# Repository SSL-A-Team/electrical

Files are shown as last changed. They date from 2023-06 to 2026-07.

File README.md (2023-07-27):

# Getting Started with A-Team Electrical

All current board releases use KiCad 7.X. 

See [releases](https://github.com/SSL-A-Team/electrical/releases) for competition production files. Our releases include known bug documentation, and the confirmed gerber, BoM, and CPL files sent to fab so you know you're looking and ordering what we did. Releases are accompanied by a tagged commit, for all editable project files used to generate the fab products.

For complex boards like control and kicker, we include spice models and python files that compute any relevant values from datasheets, and including documented references and links to needed formulations. 

## Setting Up KiCAD

### Setting Up the KiCAD Library Path
- Click `Preferences->Configure Paths`
- Under `Environment Variables` click `+`
- Set the name `LIB_DIR_AT`
- Set the path to `<repository_location>/lib` where \<repository_location\> is the download location.

Example entry:
- Name: `LIB_DIR_AT`
- Path: `C:\Users\guyfl\Documents\A-Team\electrical\lib`

### Setting Up JLCPCB Plugin

KiCAD version 6.99 (nightly) or newer should install the [KiCAD JLCPCB Tools](https://github.com/Bouni/kicad-jlcpcb-tools) plugin. 

## Setting Up the Python Environment
 1. We recommend creating a python environment using `python3 -m venv venv` (python 10 appears to be required)
 2. Install poetry `pip install poetry`
 3. Run any python file with `poetry run python <python_file>`
 4. (Optional) Add dependencies with `poetry add <dependency>`

## Soldering

Our [soldering process](SOLDERING.md) is documented. Advanced components like modern SMPS chips and current sense motor hardware proved sensitive to technique. The team's tries to PCBA as much as possible, but sometime it's too expensive to PCBA all chips, especially advanced ones not in stock at the fab house.

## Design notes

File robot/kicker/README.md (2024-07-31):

# Kicker Boards

Subfolders contain various versions of the kicker board. A summary is included below.

## Kicker Version Summary

 - v1.1.0_fe - Nonviable, check errata
 - v1.1.0_ufd - Nonviable, check errata
 - v1.0.0 - Nonviable, check errata
 - v2.0.0 - Patchable, check errata
 - v3.0 - Patchable, check errata
 - v3.1 - Functional, minor patching suggested

## KiCad Version Summary

 - v3.1 - KiCad v7.X
 - v3.0 - KiCad v7.X
 - v2.0.0 - KiCad v7.X
 - v1.1.0 - KiCad v7.X
 - v1.0.0 - KiCad v6.99 (nightly)

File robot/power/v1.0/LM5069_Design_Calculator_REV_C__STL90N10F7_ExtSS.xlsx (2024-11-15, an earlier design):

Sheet: Instructions
 | © 2014
LM5069 Design Tool- Rev. C
Typical design procedure
Typical applications require multiple passes through the design tool using MOSFET factors such as transient
thermal response and safe operating area curves. Refer to the following application reports for more detail.
Robust Hot Swap Design (http://www.ti.com/lit/pdf/slva673)
LM5069 Datasheet (See "Design-In Procedure") (http://www.ti.com/lit/gpn/lm5069)
The basic design process follows:
1. Enter operating conditions.
2. Select current limit parameters.
3. Enter MOSTFET SOA characteristics & power limit.
4. Select start up conditions (load and/or soft start). Check whether FET is operating with reasonable margin, within the SOA curve.
If not, try changing start-up conditions (soft start values, timer values), add more FETs in parallel, or switch to FET with better SOA.
5. Enter desired UVLO and OVLO values to get recommended resistor values.
6. Done
Notes
1. This worksheet is designed for use with Microsoft Excel 5.0 or later. Its use is intended to assist power supply designers in their
routine, day-to-day calculations.
2. All worksheets have light green inputs cells, white calculated cells, yellow warning cells and red high-risk cells.
3. Formulas and device constants used in the spreadsheet are locked to prohibit them from accidentally being overwritten or deleted.
TEXAS INSTRUMENTS TEXT FILE LICENSE Copyright (c) 2014 Texas Instruments Incorporated All rights reserved not granted herein. Limited License. Texas Instruments Incorporated grants a world-wide, royalty-free, non-exclusive license under copyrights and patents it now or hereafter owns or controls to make, have made, use, import, offer to sell and sell ("Utilize") this software subject to the terms herein. With respect to the foregoing patent license, such license is granted solely to the extent that any such patent is necessary to Utilize the software alone. The patent license shall not apply to any combinations which include this software, other than combinations with devices manufactured by or for TI (“TI Devices”). No hardware patent is licensed hereunder. Redistributions must preserve existing copyright notices and reproduce this license (including the above copyright notice and the disclaimer and (if applicable) source code license limitations below) in the documentation and/or other materials provided with the distribution Redistribution and use in binary form, without modification, are permitted provided that the following conditions are met: * No reverse engineering, decompilation, or disassembly of this software is permitted with respect to any software provided in binary form. * any redistribution and use are licensed by TI for use only with TI Devices. * Nothing shall obligate TI to provide you with source code for the software licensed and provided to you in obje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

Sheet: Design Calculator
LM5069 Hot Swap Design Tool
 | www.ti.com/hotswap
 |  |  | Enter Values in Green Shaded Cells
 |  |  | Calculated Values are shown in White Cells
 |  |  | Yellow and Red cells highlight potential issues with the design. Red highlights items that are higher risk.
 | Step 0: Calculator Tutorials |  | Note: Before proceeding, please watch the video tutorials listed to ensure accurate results from this tool!
 |  |  | Steps 1 & 2: Operating Conditions, Current Limit, & Circuit Breaker (7:41) (https://training.ti.com/node/1133677)
 |  |  | Step 3: MOSFET Selection (9:58) (https://training.ti.com/node/1133673)
 |  |  | Step 4: Startup (10:32) (https://training.ti.com/node/1133664)
 |  |  | Step 5: UVLO, OVLO & PGD Thresholds (4:20) (https://training.ti.com/node/1133681)
 |  |  | LM5069 Datasheet (http://www.ti.com/product/lm5069)
 |  |  | I understand and agree to watch the video tutorials if help is needed. (Choose Yes to enable the calculator.) |  |  | Yes
 |  |  | Assure to follow the layout and application guidelines listed on the datasheet. |  |  | Yes
 |  |  | *For additional questions not addressed in the videos, please post on E2E.ti.com
 | Step 1: Operating Conditions |  |  | Minimum Input Operating Voltage: VIN(MIN) | 15 | V
 |  |  |  | Nominal Input Operating Voltage: VIN(NOM) | 22.2 | V
 |  |  |  | Maximum Input Operating Voltage: VIN(MAX) | 25.2 | V
 |  |  |  | Maximum Load Current: IOUT(MAX) | 29 | A
 |  |  |  | Maximum Output Load Capacitance: CLOAD | 1500 | µF
 |  |  |  | Maximum Ambient Operating Temperature: TMAX | 45 | oC
 | Steps 1 & 2: Operating Conditions, Current Limit, & Circuit Breaker (https://training.ti.com/node/1133677)
 | Step 2: Current Limit and Circuit Breaker |  |  | Current Limit Threshold Voltage | 55 mV
 |  |  |  | Maximum Recommended Value for Effective Sense Resistance | 1.66 | mW
 |  |  |  | Use External Resistor Divider to Reduce Effecitve RS | No |  |  |  |  |  | Yes
 |  |  |  | Enter the Resistance for RS | 1.5 | mW |  |  |  |  | No
 |  |  |  | Recommended Value for RCL1 | NA | W
 |  |  |  | Recommended Value for RCL2 | NA | W
 |  |  |  | Enter value for RCL1 | 10 | W |  |  |  |  | TRUE
 | Steps 1 & 2: Operating Conditions, Current Limit, & Circuit Breaker (https://training.ti.com/node/1133677) |  |  | Enter value for RCL2 | 3.04 | W
 |  |  |  | Effective Sense Resistance (RS,EFF) | 1.50 | mW
 |  |  |  | Resulting Minimum Current Limit | 32.3 | A
 |  |  |  | Resulting Typical Current Limit | 36.7 | A
 |  |  |  | Resulting Maximum Current Limit | 41.0 | A |  |  |  |  | Retry
 |  |  |  | Maximum Power Dissipation in RS | 2.5 | W |  |  |  |  | Latch Off
 |  |  |  | Fault Response | Retry |  |  |  |  |  | 1.9 x Current Limit
 |  |  |  | Circuit Breaker to Current Limit Raitio | 1.9 x Current Limit |  |  |  |  |  | 3.9 x Current Limit
 | Step 3: MOSFET Selection |  |  | Q1 FET Name | STL90N10F7
 |  |  |  | Estimated MOSFET RQJA | 31 | oC/W |  |  |  |  | 9.978699315 | 4.193548387
 |  |  |  | Number of MosFETs | 2 | # |  |  |  |  | Values Used
 |  |  |  | MOSFET On resistance @ TJ,DC | 8 | mW |  |  |  |  | 8
 |  |  |  | Maximum FET Junction Temperature | 175 | oC |  |  |  |  | 175
 |  |  |  | 100ms SOA Current (re-use 1ms data if unavailable) @ VIN(MAX) | 55 | A |  |  |  |  | 55
 | Step 3: MOSFET Selection (https://training.ti.com/node/1133673) |  |  | 1ms SOA Current @ VIN(MAX) | 27 | A |  |  |  |  | 27
 |  |  |  | 10ms SOA Current @ VIN(MAX) | 4 | A |  |  |  |  | 4
 |  |  |  | 100ms Current at @ VIN(MAX) (enter 'NA' if not available) | NA | A |  |  |  |  | NA
 |  |  |  | 1s or DC SOA Current at @ VIN(MAX) (enter 'NA' if not available) | NA | A |  |  |  |  | NA
 | Note: TI recommends choosing a FET with SOA current specified for 100ms and/or 1s or DC. If choosing a FET without these parameters, this calculator will estimate the values via extrapolation, which leaves an inherent associated risk. |  |  | FET Power dissapation at full load (per FET) | 1.7 | W
 |  |  |  | Maximum steady state FET Junction Temperature (TJ,DC) | 97.1 | oC
 |  |  |  | Minimum Power Limit to Ensure Vsns > 5mV (PLIM,MIN) | 84.0 | W
 |  |  |  | Target Power Limit | 126.00 | W
 |  |  |  | Calculated RPWR | 23.62 | kW
 |  |  |  | Actual RPWR | 16.2 | kW | Note: Hover here to see the 3 values affecting this curve, consult a thermal expert if you are unsure!
 |  |  |  | Actual PLIM | 86.40 | W
 | Step 4: Startup |  |  | Load Turn-On Threshold | 0 | V
 |  |  |  | Startup Load Type | Constant Current
 |  |  |  | Startup Load Value | 0 | A |  |  |  |  | Constant Current
 |  |  |  | Use External Soft-Start Control (dv/dt) | Yes |  |  |  |  |  | Resistive
 |  |  |  | Typical Start Time with Vinmax (Tstart) | 157.50 | ms
 |  |  |  | IFET - ILOAD margin (lowest for Vout range) | 100%
 |  |  |  | Target Fault Timer: Tstart + Margin | 236.25 | ms
 |  |  |  | Target Timer capacitance | 5020.31 | nF
 |  |  |  | Selected Timer capacitance | 220 | nF
 |  |  |  | Final Fault Timer(Tfault) | 10.35 | ms
 | Step 4: Startup (https://training.ti.com/node/1133664) |  |  | Derated SOA / PLIM | 2.84
 |  |  |  | Can a "hot" board be hotplugged | Yes
 |  |  |  | Recommended slew Rate (max) | 0.22 | V/ms
 |  |  |  | Recommended slew Rate (min) | 0.11 | V/ms
 |  |  |  | dv/dt rate on Vout | 0.15 | V/ms
 |  |  |  | calculated SS capacitance | 106.67 | nF
 | Note: This is the typical dv/dt rate, but max value can be 1.4x. This is because the gate source current can vary from 16uA to 22uA. Thus TI recommends keeping the overall SOA margin during start-up >1.5 in order to compensate for this. |  |  | actual SS capacitance | 100 | nF
 |  |  |  | actual typical dv/dt rate on Vout | 0.16 | V/ms
 |  |  |  | SOA margin during start-up | 1.57
 |  |  |  | Target Fault Time | 0.52 | ms
 |  |  |  | Calculated Timer Capacitance | 11.05 | nF
 |  |  |  | Actual Timer Capacitance ( pick one smaller than CT,CALC) | 33 | nF
 |  |  |  | Actual Fault Time (Tfault) | 1.55 | ms
 |  |  |  | SOA margin during "hot-short" or "start-into short" | 2.84
 |  |  |  | Resulting Typical Insertion Delay Time | 24 | ms
 |  |  |  | Resulting Typical Restart Time | 310.41 | ms
 | Step 5: UVLO, OVLO & PGD Thresholds |  |  | Select Option A or Option B | Option B |  |  |  |  |  | Option A
 |  |  |  | Desired Upper UVLO Threshold | 16 | V |  |  |  |  | Option B
 |  |  |  | Desired Lower UVLO Threshold | 15 | V |  |  |  |  | Option C
 |  |  |  | Desired Upper OVLO Threshold | 30 | V |  |  |  |  | Option D
 |  |  |  | Desired Lower OVLO Threshold | 28 | V
 |  |  |  | Recommended Resistance for: R1 | 47.62 | kW
 |  |  |  | R2 | 9.52 | kW
 | Step 5: UVLO, OVLO & PGD Thresholds (https://training.ti.com/node/1133681) |  |  | R3 | 95.24 | kW
 |  |  |  | R4 | 8.66 | kW
 |  |  |  | Enter the Resistance for R1 | 47.5 | kW
 |  |  |  | Enter the Resistance for R2 | 9.53 | kW
 |  |  |  | Enter the Resistance for R3 | 95.3 | kW
 |  |  |  | Enter the Resistance for R4 | 8.66 | kW
 |  | Resulting Thresholds: | Minimum | Typical | Maximum
 |  | Resulting Upper UVLO Threshold = | 15.23 | 15.96 | 16.68 | V
 |  | Resulting Lower UVLO Threshold = | 14.66 | 14.96 | 15.26 | V
 |  | Resulting Upper OVLO Threshold = | 29.41 | 30.01 | 30.61 | V
 |  | Resulting Lower OVLO Threshold = | 26.55 | 28.01 | 29.47 | V
 |  | Note: If any of the cells above are yellow, then these values are outside of the device's operating range. This will result in the device turning either on or off at its operating limits rather than at the user selected values in yellow.
 |  |  |  | Enter the Resistance for RPG | 1500 | kW
 | Design Summary |  |  | RSNS = | 1.5 | mW
 |  |  |  | RCL1 = | DNP | W
 |  |  |  | RCL2 = | 0 | W
 |  |  |  | RPWR = | 16.2 | kW |  |  | Settings | Units
 |  |  |  | CTIMER = | 33.00 | nF |  | Current limit | 36.7 | A
 |  |  |  | R1 = | 47.5 | kW |  | Power Limit | 86.4 | W
 |  |  |  | R2 = | 9.53 | kW |  | Circuit Breaker Current | 36.7 | A
 |  |  |  | R3 = | 95.3 | kW |  | Startup Time | 157.50 | ms
 |  |  |  | R4 = | 8.66 | kW |  | Insertion Delay | 24.0 | ms
 |  |  |  | Cdv/dt = | 100 | nF |  | Fault Timeout | 1.55 | ms
 |  |  |  | CIN = | 0.01 | µF |  | Restart Time During Fault | 310.414 | ms
 |  |  |  | D1 | B380-13-F |  |  | Upper UVLO Threshold | 15.958 | V
 |  |  |  | D2 | 1N4148W-7-F |  |  | Lower UVLO Threshold | 14.961 | V
 |  |  |  | Q1 | STL90N10F7 |  |  | Upper OVLO Threshold | 30.012 | V
 |  |  |  | Q2 | MMBT5401LT1G |  |  | Lower OVLO Threshold | 28.010 | V
 |  |  |  | Z1 | 5.0SMDxx
 | Notes: | 1. Although not mandatory, CIN provides transient suppression at the VIN pin
 |  | 2. A TVS clamp from VIN to GND is absolutely mandatory to clamp the voltage overshoot upon MOSFET turn-off, e.g. during circuit breaker
 |  | 3. Componet tolerances not accounted for in Min/Max Calculations.

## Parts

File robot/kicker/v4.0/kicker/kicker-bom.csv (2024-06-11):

Comment | Designator | Footprint
10u 100V | C1, C2 | Capacitor_SMD:C_1210_3225Metric
100n 50V | C3, C4, C5, C26, C29, C34, C35, C36, C37, C38, C40, C41, C46, C48, C49, C54, C55, C56, C57, C58, C59, C61, C68, C69 | Capacitor_SMD:C_0402_1005Metric
4.7n 63V | C6 | Capacitor_SMD:C_0402_1005Metric
10n 6.3V | C7, C8, C45, C47 | Capacitor_SMD:C_0402_1005Metric
470n 6.3V | C9, C10 | Capacitor_SMD:C_0402_1005Metric
1n 50V | C11, C12, C13, C14 | Capacitor_SMD:C_0402_1005Metric
1u 50V | C15, C16, C17, C18, C23, C24, C25, C39 | Capacitor_SMD:C_0402_1005Metric
10u 25V | C19, C20, C21, C22 | Capacitor_SMD:C_0603_1608Metric
11pF | C27, C28 | Capacitor_SMD:C_0402_1005Metric
4.7u 6.3V | C30, C31, C32, C33, C44 | Capacitor_SMD:C_0402_1005Metric
15pF | C42, C43 | Capacitor_SMD:C_0402_1005Metric
10u 6.3V | C50 | Capacitor_SMD:C_0402_1005Metric
1000uF 200V | C51, C52, C53 | Capacitor_THT:CP_Radial_D25.0mm_P10.00mm_SnapIn
10u 50V | C60, C64, C66, C67, C70, C72 | Capacitor_SMD:C_0805_2012Metric
220u 50V | C62, C63 | Capacitor_SMD:CP_Elec_10x10
10n 50V | C65 | Capacitor_SMD:C_0402_1005Metric
6.8n 50V | C71 | Capacitor_SMD:C_0402_1005Metric
4.7u 50V | C73 | Capacitor_SMD:C_0805_2012Metric
100n 200V | C74 | Capacitor_SMD:C_0805_2012Metric
100n 500V | C75 | Capacitor_SMD:C_1210_3225Metric
470n 500V | C76, C77 | Capacitor_SMD:C_1812_4532Metric
824521261 | D1, D2 | AT-Discrete:D_SMB_Non-Polar
XL-1608UWC-04 | D3 | AT-LED:LED0603
DSS14U | D4, D5, D6, D7 | Diode_SMD:D_SOD-123F
XL-1608SURC-06 | D8, D13 | AT-LED:LED0603
PESD3V3L5UY | D9 | Package_TO_SOT_SMD:SOT-363_SC-70-6
XL-1608UBC-04 | D10, D11 | AT-LED:LED0603
XL-1608UGC-04 | D12 | AT-LED:LED0603
XL-1608UOC-06 | D14 | AT-LED:LED0603
APA1606SURCK | D15, D16 | AT-LED:APA1606
MURS460 | D17, D18 | Diode_SMD:D_SMC
HS5M | D19 | Diode_SMD:D_SMC
15A | F1 | AT-Fuses:3557-2
1.0A | F2, F3, F4, F5 | Fuse:Fuse_0603_1608Metric
9774005243R | H3, H4, H7, H8 | AT-Mechanical:WE-9774005243R
Conn_ARM_JTAG_SWD_10 | J2 | AT-Connectors:Samtec-2x5pin-0.5mm
Conn_01x02 | J3 | Connector_JST:JST_SH_SM02B-SRSS-TB_1x02-1MP_P1.00mm_Horizontal
Conn_01x04_Pin | J4 | Connector_PinHeader_2.54mm:PinHeader_1x04_P2.54mm_Vertical
Conn_01x10 | J5, J6, J9, J16 | Connector_JST:JST_SH_SM10B-SRSS-TB_1x10-1MP_P1.00mm_Horizontal
Conn_01x02 | J7, J8 | AT-Connectors:2157601002
Conn_01x02 | J10 | AT-JST_PA:SM02B-PASS-TBT
Conn_01x08 | J11, J14, J15 | Connector_JST:JST_SH_SM08B-SRSS-TB_1x08-1MP_P1.00mm_Horizontal
Conn_01x03 | J12, J13 | Connector_JST:JST_SH_SM03B-SRSS-TB_1x03-1MP_P1.00mm_Horizontal
ASPI-6045S-220M-T | L1 | AT-Inductors:ASPI-6045S
SDCHA1V5040-150-R | L2, L3, L4, L5 | AT-Inductors:SDCHA1V50
650 @100MHz | L6 | Resistor_SMD:R_0603_1608Metric
GA3460-BL | L7 | AT-Inductors:GA34XX-BL
USB_C_Plug_USB2.0 | P1 | Connector_USB:USB_C_Receptacle_Molex_105450-0101
BSS138K | Q1, Q5 | Package_TO_SOT_SMD:SOT-23
SQJA80EP-T1_GE3 | Q2, Q3 | AT-Discrete:PowerPAK_SO-8L_Single
SI2310-TP | Q4 | Package_TO_SOT_SMD:SOT-23
IXGA48N60A3 | Q6, Q7 | Package_TO_SOT_SMD:TO-263-2
BSC0402NSATMA1 | Q8 | Package_TO_SOT_SMD:TDSON-8-1
1 | R1, R2 | Resistor_SMD:R_2512_6332Metric
1.47M | R3, R69, R70, R71, R72 | Resistor_SMD:R_0805_2012Metric
1k | R4, R6, R24, R25, R26, R27, R83 | Resistor_SMD:R_0402_1005Metric
10k | R5, R13, R23, R29, R31, R33, R35, R37, R39, R41, R43, R47, R52, R53, R54, R55, R58, R59, R61, R63, R64, R65, R66, R67, R68, R77, R78, R94, R95, R102, R103 | Resistor_SMD:R_0402_1005Metric
10M | R7 | Resistor_SMD:R_0402_1005Metric
1.5M | R8, R15, R16 | Resistor_SMD:R_0402_1005Metric
69.8k | R9 | Resistor_SMD:R_0402_1005Metric
232k | R10 | Resistor_SMD:R_0402_1005Metric
10 | R11, R12, R20, R81, R82, R88 | Resistor_SMD:R_0402_1005Metric
5.1k | R14 | Resistor_SMD:R_0603_1608Metric
100k | R17, R18, R57, R79, R80, R87 | Resistor_SMD:R_0402_1005Metric
23.2k 1% | R19 | Resistor_SMD:R_0402_1005Metric
4.7k | R21 | Resistor_SMD:R_0402_1005Metric
210k | R22 | Resistor_SMD:R_0402_1005Metric
140k | R28, R84 | Resistor_SMD:R_0402_1005Metric
31.6k | R30 | Resistor_SMD:R_0402_1005Metric
53.6k | R32 | Resistor_SMD:R_0402_1005Metric
68.1k | R34 | Resistor_SMD:R_0402_1005Metric
110k | R36 | Resistor_SMD:R_0402_1005Metric
23.2k | R38 | Resistor_SMD:R_0402_1005Metric
40.2k | R40 | Resistor_SMD:R_0402_1005Metric
52.3k | R42 | Resistor_SMD:R_0402_1005Metric
5.1k | R44, R45, R60 | Resistor_SMD:R_0402_1005Metric
10.7k | R46 | Resistor_SMD:R_0402_1005Metric
330 | R48, R49, R50, R51, R56, R76 | Resistor_SMD:R_0402_1005Metric
1M | R62 | Resistor_SMD:R_0402_1005Metric
475k | R73, R74 | Resistor_SMD:R_0805_2012Metric
4.75k | R75 | Resistor_SMD:R_0402_1005Metric
22k | R85 | Resistor_SMD:R_0402_1005Metric
1 | R86 | Resistor_SMD:R_0805_2012Metric
4m | R89, R90 | Resistor_SMD:R_1206_3216Metric
976k 0.1% | R91, R92 | Resistor_SMD:R_0805_2012Metric
17.4k 0.1% | R93 | Resistor_SMD:R_0402_1005Metric
2.1k | R96, R97, R98, R99, R100, R101 | Resistor_SMD:R_0402_1005Metric
ACFG1 | RV1 | Potentiometer_SMD:Potentiometer_Bourns_3269X_Horizontal
ACFG2 | RV2 | Potentiometer_SMD:Potentiometer_Bourns_3269X_Horizontal
PWR_ON | SW1 | Button_Switch_SMD:SW_SPST_TL3305A
BTN0 | SW2 | Button_Switch_SMD:SW_SPST_TL3305A
SW_DIP_x04 | SW3 | at-switches:CHP-041TB
RST | SW4 | Button_Switch_SMD:SW_SPST_TL3305A
LTC4367 | U1 | AT-IC:MS8
LTC2955-1 | U2 | AT-IC:LTC2955-TS8
ITS4140N | U3 | Package_TO_SOT_SMD:SOT-223
LT3504 | U4 | AT-IC:UFD
STM32F407VETx | U5 | Package_QFP:LQFP-100_14x14mm_P0.5mm
SK9822 | U6, U8 | AT-LED:SK9822
AT25DF041x-UxN-x | U7 | Package_SO:SOIC-8_3.9x4.9mm_P1.27mm
AD8494 | U9 | Package_SO:MSOP-8_3x3mm_P0.65mm
ISO6720-Q1 | U10, U12 | AT-IC:ISO672X
ISO6721-Q1 | U11 | AT-IC:ISO672X
IX4427 | U13 | Package_SO:SOIC-8_3.9x4.9mm_P1.27mm
LT3757EMSE | U14 | Package_SO:MSOP-10-1EP_3x3mm_P0.5mm_EP1.68x1.88mm
TAXM8M4RDBCCT2T | Y1 | Crystal:Crystal_SMD_3225-4Pin_3.2x2.5mm
Q13FC13500005 | Y2 | Crystal:Crystal_SMD_3215-2Pin_3.2x1.5mm

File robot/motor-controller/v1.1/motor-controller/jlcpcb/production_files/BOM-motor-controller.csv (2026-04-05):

Comment | Designator | Footprint | LCSC | Quantity
0 | R33,R39,R41,R42 | R_0402_1005Metric | C17168 | 4
0.1uF 63V | C1,C13,C14,C16,C4,C6,C7,C9 | C_0402_1005Metric | C131394 | 8
0467.250NRHF | F3 | Fuse_0603_1608Metric_Pad1.05x0.95mm_HandSolder | C151137 | 1
0501010.WR1 | F2 | Fuse_1206_3216Metric_Pad1.42x1.75mm_HandSolder | C207003 | 1
06F-0200L1 | F1,F4 | Fuse_0603_1608Metric_Pad1.05x0.95mm_HandSolder | C377220 | 2
10 | R1,R10,R11,R14,R4,R5 | R_0402_1005Metric | C25077 | 6
100k | R20,R34,R37 | R_0402_1005Metric | C25741 | 3
10k | R15,R16,R28,R29,R30,R31,R32,R40,R44,R7,R8 | R_0402_1005Metric | C60490 | 11
11.5k | R17 | R_0402_1005Metric | C270653 | 1
11pF | C20,C21 | C_0402_1005Metric | C161525 | 2
13.7k 1% | R19 | R_0402_1005Metric | C852522 | 1
15.0k 1% | R36 | R_0402_1005Metric | C853539 | 1
15pF | C18,C19 | C_0402_1005Metric | C86285 | 2
165k 1% | R23 | R_0402_1005Metric | C1509613 | 1
1k | R38 | R_0402_1005Metric | C11702 | 1
1k 1% |  | R_0402_1005Metric | C11702 | 0
1uF 10V | C11,C12,C15,C17,C3,C5 | C_0402_1005Metric | C14445 | 6
1uF 63V | C2,C8 | C_1206_3216Metric | C70463 | 2
2.49k 1% | R22,R24,R26 | R_0402_1005Metric | C852700 | 3
22uF 6.3V | C10 | C_0402_1005Metric | C415703 | 1
30k 1% |  | R_0402_1005Metric | C25776 | 0
330 | R35 | R_0402_1005Metric | C25104 | 1
62 | R12,R13,R2,R3,R6,R9 | R_0402_1005Metric | C100501 | 6
62 1% | R25 | R_0402_1005Metric | C852875 | 1
650 @100MHz | L1 | R_0603_1608Metric | C21189 | 1
AS5047P | U2 | TSSOP-14_4.4x5mm_P0.65mm | C962063 | 1
BAS16VY | D1,D2 | SOT-363_SC-70-6 | C135826 | 2
BM03B-ACHFKS | J2 | JST_ACHFR_03V | C5177195 | 1
BM06B-ACHFKS | J4 | JST_ACHFR_06V | C5304907 | 1
BSS138K | Q7 | SOT-23 | C5224263 | 1
Conn_ARM_JTAG_SWD_10 | J6 | Samtec-2x5pin-1.27mm | C448647 | 1
EEEFT1V101AP | C22,C23 | CP_Elec_6.3x5.8 | C128464 | 2
HoLLR2512-3W-100mR-1% | R18,R27 | 2512_CS_ADI-TypeC | C2994646 | 2
Q13FC13500005 | Y1 | Crystal_SMD_3215-2Pin_3.2x1.5mm | C841881 | 1
SM06B-SRSS-TB | J3 | JST_SH_SM06B-SRSS-TB_1x06-1MP_P1.00mm_Horizontal | C160405 | 1
SMBJ26CA | D6 | D_SMB_Non-Polar | C135063 | 1
SMF3.3CA | D7 | D_SOD-123 | C6165153 | 1
STL90N10F7 | Q1,Q2,Q3,Q4,Q5,Q6 | PowerFLAT_5x6 | C457493 | 6
STSPIN32F0B | U1 | QFN-48-1EP_7x7mm_P0.5mm_EP2.8x2.8mm | C1521053 | 1
TAXM8M4RDBCCT2T | Y2 | Crystal_SMD_3225-4Pin_3.2x2.5mm | C400090 | 1
TLV70030_SOT353 | U3 | SOT-353_SC-70-5 | C527437 | 1
XL-1608SURC-06 | D5 | LED0603 | C965799 | 1
XL-1608UGC-04 | D4 | LED0603 | C965804 | 1
XL-1608UOC-06 | D3 | LED0603 | C965800 | 1
SM12B-ZESS | J5 | JST_ZE_SM12B-ZESS-TB_1x12-1MP_P1.50mm_Horizontal |  | 1

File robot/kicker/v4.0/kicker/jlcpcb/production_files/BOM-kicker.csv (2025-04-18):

Comment | Designator | Footprint | LCSC | Quantity
26.1k | R8 | R_0402_1005Metric | C102932 | 1
330 | R1,R12,R13,R14,R15,R2,R20,R70,R78,R79,R85 | R_0402_1005Metric | C105875 | 11
0 | R24,R28,R6 | R_0402_1005Metric | C106231 | 3
1k | R29,R34,R37,R40,R42,R58,R9 | R_0402_1005Metric | C11702 | 7
10 | R56,R57,R63 | R_0402_1005Metric | C138066 | 3
0467.250NRHF | F5 | Fuse_0603_1608Metric_Pad1.05x0.95mm_HandSolder | C151137 | 1
1u 50V | C11,C17,C3 | C_0402_1005Metric | C1518208 | 3
11pF | C21,C23 | C_0402_1005Metric | C161525 | 2
4.7u 50V | C39 | C_0805_2012Metric | C162420 | 1
23.2k | R38 | R_0402_1005Metric | C163477 | 1
1u | C2 | C_1206_3216Metric | C1848 | 1
~ | F1,F2 | Fuse_0603_1608Metric_Pad1.05x0.95mm_HandSolder | C187605 | 2
1.47M | R4,R45,R46,R47,R48,R49,R50 | R_0805_2012Metric | C189666 | 7
650 @100MHz | L1 | R_0603_1608Metric | C21189 | 1
976k 0.1% | R66,R67 | R_0805_2012Metric | C229056 | 2
BSS138K | Q1,Q2 | SOT-23 | C255592 | 2
22k | R60 | R_0402_1005Metric | C25768 | 1
14.7k | R51 | R_0402_1005Metric | C25856 | 1
1.5k | R39 | R_0402_1005Metric | C25867 | 1
2.1k | R72,R73,R74,R75 | R_0402_1005Metric | C25877 | 4
SM08B-GHS-TB | J8,J9 | JST_GH_SM08B-GHS-TB_1x08-1MP_P1.25mm_Horizontal | C265111 | 2
BM04B-PASS-1-TFT | J2 | JST_PA_BM04B-PASS_1x04_P2.00_Vertical | C265298 | 1
JST-SM10B-GHS | J1,J11 | JST_GH_SM10B-GHS-TB_1x10-1MP_P1.25mm_Horizontal | C2683602 | 2
140k | R59 | R_0402_1005Metric | C270645 | 1
11.5k | R33 | R_0402_1005Metric | C270653 | 1
8.06k | R36 | R_0402_1005Metric | C276278 | 1
SK9822 | U4,U6 | SK9822 | C2829089 | 2
BTN0 | SW1,SW3 | SW_SPST_TL3305A | C2886902 | 2
1 | R61 | R_0805_2012Metric | C2907233 | 1
1N4001 | D2 | D_SMA | C2909965 | 1
HS5M | D14 | D_SMC | C2944264 | 1
0.1u | C1,C10,C12,C13,C14,C15,C16,C18,C24,C28,C34,C35,C6,C7 | C_0402_1005Metric | C307331 | 14
10A | F3 | 3557-2 | C352820 | 1
824521261 | D1 | D_SMB_Non-Polar | C3708253 | 1
06F-0200L1 | F4 | Fuse_0603_1608Metric_Pad1.05x0.95mm_HandSolder | C377220 | 1
TAXM8M4RDBCCT2T | Y2 | Crystal_SMD_3225-4Pin_3.2x2.5mm | C400090 | 1
STM32G474VETx | U3 | LQFP-100_14x14mm_P0.5mm | C431632 | 1
10u 50V | C27,C30,C32,C33,C36,C38,C5 | C_0805_2012Metric | C440198 | 7
100n 500V | C41 | C_1210_3225Metric | C440207 | 1
Conn_ARM_JTAG_SWD_10 | J4 | Samtec-2x5pin-1.27mm | C448647 | 1
PE1206FRM470R008L | R64,R65 | R_1206_3216Metric | C473031 | 2
PESD3V3L5UY | D3 | SOT-363_SC-70-6 | C477992 | 1
17.4k 0.1% | R68 | R_0402_1005Metric | C517755 | 1
TPS7B86 | U2 | Texas_HSOP-8-1EP_3.9x4.9mm_P1.27mm | C5189739 | 1
TLV70030_SOT353 | U1 | SOT-353_SC-70-5 | C527437 | 1
LT3757EMSE | U8 | MSOP-10-1EP_3x3mm_P0.5mm_EP1.68x1.88mm | C580135 | 1
IX4427 | U7 | SOIC-8_3.9x4.9mm_P1.27mm | C5804604 | 1
10k | R10,R11,R16,R17,R18,R19,R25,R26,R27,R30,R31,R32,R35,R43,R44,R52,R53,R7 | R_0402_1005Metric | C60490 | 18
100k | R21,R3,R54,R55,R62,R69,R71,R76,R77,R80,R81,R82,R83,R84,R86,R87 | R_0402_1005Metric | C60491 | 16
4.7u 6.3V | C19,C8 | C_0402_1005Metric | C76995 | 2
10n 50V | C31,C4,C9 | C_0402_1005Metric | C77019 | 3
100n 200V | C40 | C_0805_2012Metric | C784084 | 1
649 | R41 | R_0402_1005Metric | C82294 | 1
Q13FC13500005 | Y1 | Crystal_SMD_3215-2Pin_3.2x1.5mm | C841881 | 1
15pF | C20,C22 | C_0402_1005Metric | C88877 | 2
6.8n 50V | C37 | C_0402_1005Metric | C93654 | 1
MURS460 | D12,D13 | D_SMC | C961891 | 2
XL-1608SURC-06 | D10,D11,D7 | LED0603 | C965799 | 3
XL-1608UOC-06 | D9 | LED0603 | C965800 | 1
XL-1608UGC-04 | D5 | LED0603 | C965804 | 1
XL-1608UBC-04 | D4,D6 | LED0603 | C965807 | 2
XL-1608UWC-04 | D8 | LED0603 | C965808 | 1
5v0 US | TP1 | TestPoint_Pad_D1.0mm |  | 1
2165711002 | J6 | 2165711002 |  | 1
2165711002 | J5 | 2165711002 |  | 1
ESMQ201VSN152MR35S | C26 | CP_Radial_D30.0mm_P10.00mm_SnapIn |  | 1
ESMQ201VSN152MR35S | C25 | CP_Radial_D30.0mm_P10.00mm_SnapIn |  | 1
GA3460-BL | L2 | GA34XX-BL |  | 1
IXGA48N60A3 | Q3 | TO-263-2 |  | 1
IXGA48N60A3 | Q4 | TO-263-2 |  | 1
3v3 US | TP2 | TestPoint_Pad_D1.0mm |  | 1
SW_DIP_x04 | SW2 | CHP-041TB |  | 1
BSC0402NSATMA1 | Q5 | TDSON-8-1 |  | 1
REH1020471M050K | C29 | CP_Radial_H_InPlane_D10.00mm_H22.00mm_P5.00mm |  | 1
3269P-1-103GLF | RV1 | Potentiometer_Bourns_3269P_Horizontal |  | 1
3269P-1-103GLF | RV2 | Potentiometer_Bourns_3269P_Horizontal |  | 1
SM12B-ZESS-TB | J7 | JST_ZE_BM12B-ZESS-TBT_1x12-1MP_P1.50mm_Vertical |  | 1

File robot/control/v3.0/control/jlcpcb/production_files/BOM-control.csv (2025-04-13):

Comment | Designator | Footprint | LCSC | Quantity
1k | R12,R13,R14,R5,R6 | R_0402_1005Metric | C11702 | 5
SMBJ26CA | D1 | D_SMB_Non-Polar | C123932 | 1
LTST-C195KGJRKT | D3,D4,D6,D7 | LED0606_S_1324 | C125104 | 4
USB_C_Plug_USB2.0 | P1 | USB_C_Receptacle_Molex_105450-0101 | C134092 | 1
1u 50V | C2,C6,C8,C9 | C_0402_1005Metric | C1518208 | 4
650 @100MHz | L1 | R_0603_1608Metric | C15402 | 1
15pF | C3,C4 | C_0402_1005Metric | C1548 | 2
2.2uF 10V | C14,C15 | C_0603_1608Metric | C1607 | 2
11pF | C11,C12 | C_0402_1005Metric | C161525 | 2
0.1uF 63V | C28,C29,C30,C32,C33,C34,C35,C36,C37 | C_0402_1005Metric | C162178 | 9
4.7uF 25V | C38 | C_0805_2012Metric | C1779 | 1
1u | C31 | C_1206_3216Metric | C1848 | 1
Conn_01x06 | J14 | JST_GH_BM06B-GHS-TBT_1x06-1MP_P1.25mm_Vertical | C189892 | 1
JST-GH-SM05B | J12 | JST_GH_SM05B-GHS-TB_1x05-1MP_P1.25mm_Horizontal | C189896 | 1
10 | R91 | R_0402_1005Metric | C25077 | 1
330 | R1,R107,R114,R115,R117,R122,R123,R18,R19,R22,R23,R28,R29,R34,R35,R40,R41,R46,R47,R52,R53,R58,R59,R60,R63,R64,R74,R75,R84,R85,R86,R89,R90,R92,R93,R94,R95,R97 | R_0402_1005Metric | C25104 | 38
BSS138K | Q2,Q4 | SOT-23 | C255592 | 2
100k | R119,R120,R121,R124,R125,R16,R17,R20,R21,R26,R27,R30,R31,R32,R33,R36,R37,R38,R39,R4,R42,R43,R44,R45,R48,R49,R50,R51,R54,R55,R56,R7,R8 | R_0402_1005Metric | C25741 | 33
10k | R100,R101,R102,R103,R104,R105,R106,R108,R109,R110,R111,R112,R113,R116,R118,R24,R25,R3,R65,R66,R67,R68,R69,R70,R71,R72,R73,R76,R77,R78,R79,R80,R81,R82,R83,R87,R88,R96,R98,R99 | R_0402_1005Metric | C25744 | 40
1.5k | R10 | R_0402_1005Metric | C25867 | 1
2.7k | R61,R62 | R_0402_1005Metric | C25885 | 2
5.1k | R126,R15 | R_0402_1005Metric | C25905 | 2
Conn_01x04 | J13 | JST_PA_SM04B-PASS_1x04_P2.00mm_Horizontal | C265073 | 1
BM10B-SRSS-TB | J5 | JST_SH_BM10B-SRSS-TB_1x10-1MP_P1.00mm_Vertical | C265443 | 1
Conn_01x10_MountingPin | J10,J9 | JST_GH_SM10B-GHS-TB_1x10-1MP_P1.25mm_Horizontal | C2683602 | 2
11.5k | R9 | R_0402_1005Metric | C270653 | 1
MHT194YBCT | D5 | LED0606_Z_1324 | C2764891 | 1
SK9822 | U10,U11,U12,U13,U14,U4,U5,U6,U7,U8,U9 | SK9822 | C2829089 | 11
219-8MST | SW6 | 219-8MST | C2842674 | 1
RST | SW2 | SW_SPST_TL3305A | C2886902 | 1
~ | F6,F7 | Fuse_0603_1608Metric_Pad1.05x0.95mm_HandSolder | C2924957 | 2
SW_DIP_x02 | SW3 | 219-2MST | C2961978 | 1
SW_DIP_x02 | SW5 | 219-2MST | C314502 | 1
23.7k | R57 | R_0402_1005Metric | C327362 | 1
06F-0200L1 | F8 | Fuse_0603_1608Metric_Pad1.05x0.95mm_HandSolder | C377220 | 1
TAXM8M4RDBCCT2T | Y2 | Crystal_SMD_3225-4Pin_3.2x2.5mm | C400090 | 1
Conn_ARM_JTAG_SWD_10 | J2 | Samtec-2x5pin-1.27mm | C448647 | 1
RBR5LAM60ATR | D9 | D_SOD-128 | C509955 | 1
TLV70030_SOT353 | U3 | SOT-353_SC-70-5 | C527437 | 1
BMI323 | U2 | BMI323 | C5368700 | 1
4A | F1,F2,F3,F4 | Fuse_1206_3216Metric_Pad1.42x1.75mm_HandSolder | C5383193 | 4
A6SN-1104 | SW1 | SW_DIP_SPSTx01_Slide_Omron_A6S-110x_W8.9mm_P2.54mm | C600988 | 1
SI2310-TP | Q3 | SOT-23 | C669000 | 1
STM32H723ZGTx | U1 | LQFP-144_20x20mm_P0.5mm | C730146 | 1
100n 50V | C1,C10,C13,C16,C17,C18,C19,C20,C21,C22,C23,C24,C25,C26,C27,C5,C7 | C_0402_1005Metric | C77020 | 17
650 | R11 | R_0402_1005Metric | C82294 | 1
Q13FC13500005 | Y1 | Crystal_SMD_3215-2Pin_3.2x1.5mm | C841881 | 1
BSS84 | Q1 | SOT-23 | C85202 | 1
B3F-1000 | SW10,SW11,SW12,SW7,SW8,SW9 | B3F-1000 | C93157 | 6
MLT-5020 | BZ1 | MLT-5020 | C95297 | 1
XL-1608UOC-06 | D8 | LED0603 | C965800 | 1
XL-1608UGC-04 | D10,D11,D12,D13 | LED0603 | C965804 | 4
XL-1608UWC-04 | D2 | LED0603 | C965808 | 1
SM12B-ZESS | J6 | JST_ZE_SM12B-ZESS-TB_1x12-1MP_P1.50mm_Horizontal |  | 1
221ADC16 | SW4 | 221ADC16 |  | 1
SM12B-ZESS | J8 | JST_ZE_SM12B-ZESS-TB_1x12-1MP_P1.50mm_Horizontal |  | 1
SM12B-ZESS | J3 | JST_ZE_SM12B-ZESS-TB_1x12-1MP_P1.50mm_Horizontal |  | 1
SM12B-ZESS | J7 | JST_ZE_SM12B-ZESS-TB_1x12-1MP_P1.50mm_Horizontal |  | 1
BM11B-SRSS-TB | J4 | JST_SH_BM11B-SRSS-TB_1x11-1MP_P1.00mm_Vertical |  | 1
Conn_02x05_Odd_Even | J15 | PinHeader_2x05_P2.54mm_Vertical |  | 1
MEM2067-02-180-00-A | J1 | MEM2067-02-180-00-A |  | 1

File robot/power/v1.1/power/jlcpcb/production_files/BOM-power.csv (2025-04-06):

Comment | Designator | Footprint | LCSC | Quantity
TLV70033_SOT23-5 | U9 | SOT-23-5 | C11337 | 1
68.1k | R30 | R_0402_1005Metric | C11537 | 1
1k | R16,R21,R9 | R_0402_1005Metric | C11702 | 3
3.6M | R64 | R_0402_1005Metric | C131575 | 1
1.5M | R17,R19,R2,R20,R22,R41,R42,R43 | R_0402_1005Metric | C138034 | 8
1n | C28,C29 | C_0402_1005Metric | C14442 | 2
0467.250NRHF | F4 | Fuse_0603_1608Metric_Pad1.05x0.95mm_HandSolder | C151137 | 1
0467.500NRHF | F5 | Fuse_0603_1608Metric_Pad1.05x0.95mm_HandSolder | C151138 | 1
10n | C41 | C_0402_1005Metric | C15195 | 1
LMR14050 | U6,U7,U8 | SOIC-8-1EP_3.9x4.9mm_P1.27mm_EP2.29x3mm | C155484 | 3
Conn_01x07 | J8 | JST_XH_S7B-XH-A_1x07_P2.50mm_Horizontal | C157916 | 1
5.6pF | C39 | C_0402_1005Metric | C161329 | 1
100n 63V | C10,C11,C14,C21,C26,C27,C38,C43,C5,C8,C9 | C_0402_1005Metric | C162178 | 11
FXL1040-8R2-M | L2,L3 | L_Bourns_SRP1038C_10.0x10.0mm | C167232 | 2
220n | C45,C49,C51,C52,C53,C54,C55 | C_0402_1005Metric | C16772 | 7
FNR4030S470MT | L4 | L_Changjiang_FNR4030S | C167888 | 1
0 | R25,R27,R55 | R_0402_1005Metric | C17168 | 3
1u 63V | C13,C42 | C_1206_3216Metric | C1848 | 2
SM02B-GHS | SW2 | JST_GH_SM02B-GHS-TB_1x02-1MP_P1.25mm_Horizontal | C189893 | 1
SM05B-GHS | J6 | JST_GH_SM05B-GHS-TB_1x05-1MP_P1.25mm_Horizontal | C189896 | 1
650 @100MHz | L1 | R_0603_1608Metric | C19330 | 1
MMBT5401LT1G | Q6 | SOT-23 | C231274 | 1
4.7u 10V | C6,C7 | C_0402_1005Metric | C23733 | 2
1.5n | C30 | C_0402_1005Metric | C23967 | 1
10 | R8 | R_0402_1005Metric | C25077 | 1
330 | R44,R45,R46,R47,R48,R49 | R_0402_1005Metric | C25104 | 6
12k | R34 | R_0402_1005Metric | C25752 | 1
133k | R74 | R_0402_1005Metric | C25753 | 1
150k | R72 | R_0402_1005Metric | C25755 | 1
499k | R51,R61,R63,R65,R67,R69,R71 | R_0402_1005Metric | C25793 | 7
549k | R70 | R_0402_1005Metric | C25795 | 1
56k | R52 | R_0402_1005Metric | C25796 | 1
47.5k | R10 | R_0402_1005Metric | C25896 | 1
4.99k | R53,R57,R59,R77 | R_0402_1005Metric | C25903 | 4
100p | C46,C47,C48,C50 | C_0402_1005Metric | C26409 | 4
LM5069 | U4 | VSSOP-10_3x3mm_P0.5mm | C2653582 | 1
29.4k | R76 | R_0402_1005Metric | C26973 | 1
52.3k | R39 | R_0402_1005Metric | C26982 | 1
69.8k | R29 | R_0402_1005Metric | C26985 | 1
76.8k | R37 | R_0402_1005Metric | C26987 | 1
95.3k | R12 | R_0402_1005Metric | C26990 | 1
9.31k | R56 | R_0402_1005Metric | C270572 | 1
8.66k | R13 | R_0402_1005Metric | C270576 | 1
4.75M | R62 | R_0402_1005Metric | C270598 | 1
16.2k | R18 | R_0402_1005Metric | C27176 | 1
SK9822 | U1,U2 | SK9822 | C2829089 | 2
RST | SW1,SW3 | SW_SPST_TL3305A | C2886899 | 2
3v3 Local Enable | JP2,JP3 | R_0603_1608Metric_Pad0.98x0.95mm_HandSolder | C2907080 | 2
180u | C22,C25,C32,C35 | CP_Elec_6.3x7.7 | C2918361 | 4
V25PN60 | D1,D11,D15,D16 | TO-277A | C3018534 | 4
8.2n | C23,C24,C31 | C_0402_1005Metric | C307436 | 3
23.7k | R6 | R_0402_1005Metric | C327362 | 1
15A | F6 | 3557-2 | C352820 | 1
68k | R33 | R_0402_1005Metric | C36871 | 1
165k | R38 | R_0402_1005Metric | C38706 | 1
TAXM8M4RDBCCT2T | Y1 | Crystal_SMD_3225-4Pin_3.2x2.5mm | C400090 | 1
330u | C33,C36 | CP_Elec_6.3x7.7 | C413522 | 2
33n 50V | C12 | C_0402_1005Metric | C415530 | 1
10u 50V | C15,C18,C34 | C_0805_2012Metric | C440198 | 3
STL90N10F7 | Q4,Q5 | PowerFLAT_5x6 | C457493 | 2
2.67M | R66 | R_0402_1005Metric | C477658 | 1
PESD3V3L5UY | D7,D8,D9 | SOT-363_SC-70-6 | C477992 | 3
34k | R35 | R_0402_1005Metric | C48939 | 1
SM02B-PASS | J10 | JST_PA_SM02B-PASS_1x02_P2.00mm_Horizontal | C495198 | 1
1.5m | R14,R15 | R_2512_6332Metric | C500737 | 2
RBR5LAM60ATR | D18,D6 | D_SOD-128 | C509955 | 2
SM03B-GHS | J2 | JST_GH_SM03B-GHS-TB_1x03-1MP_P1.25mm_Horizontal | C514175 | 1
FTSH-105-01-L-DV-K-TR | J1 | Samtec-2x5pin-1.27mm | C5155080 | 1
TPS54260DGQ | U10 | HVSSOP-10-1EP_3x3mm_P0.5mm_EP1.57x1.88mm | C51800 | 1
4.42k | R58 | R_0402_1005Metric | C52269 | 1
STM32G030C8Tx | U3 | LQFP-48_7x7mm_P0.5mm | C529329 | 1
APH1265T220M | L5 | L_APV_APH1265 | C5349635 | 1
1.6M | R68 | R_0402_1005Metric | C57065 | 1
0466005.NRHF | F1,F2,F3 | Fuse_1206_3216Metric_Pad1.42x1.75mm_HandSolder | C57525 | 3
10k | R23,R28,R3,R31,R32,R36,R4,R40,R5,R7,R73,R75 | R_0402_1005Metric | C60490 | 12
SI2310-TP | Q2 | SOT-23 | C669000 | 1
LTC2955-2 | U5 | TSOT-23-8_HandSoldering | C683797 | 1
11pF | C1,C3 | C_0402_1005Metric | C710643 | 2
SMBJ28CA | D10,D12 | D_SMB_Non-Polar | C78417 | 2
BSS84 | Q1 | SOT-23 | C82079 | 1
1N4148W | D13 | D_SOD-123 | C83528 | 1
Q13FC13500005 | Y2 | Crystal_SMD_3215-2Pin_3.2x1.5mm | C841881 | 1
47u 10V | C44 | C_1210_3225Metric | C84494 | 1
2.7n | C40 | C_0402_1005Metric | C84704 | 1
2N7002 | Q3 | SOT-23 | C8545 | 1
15pF | C2,C4 | C_0402_1005Metric | C86285 | 2
1N4001 |  | D_SMA | C895212 | 0
MLT-5020 | BZ1 | MLT-5020 | C95297 | 1
9.53k | R11 | R_0402_1005Metric | C96273 | 1
XL-1608SURC-06 | D3 | LED0603 | C965799 | 1
XL-1608UOC-06 | D4 | LED0603 | C965800 | 1
XL-1608UGC-04 | D2 | LED0603 | C965804 | 1
XL-1608UWC-04 | D5 | LED0603 | C965808 | 1
5.6M | R50,R60 | R_0402_1005Metric | C966764 | 2
4.7u 50V | C16,C17,C19,C20,C37 | C_0805_2012Metric | C98192 | 5
SM04B-PASS | J4 | JST_PA_SM04B-PASS_1x04_P2.00mm_Horizontal |  | 1
OVLO | TP3 | TestPoint_Pad_D2.5mm |  | 1
XT30PW-F | J3 | AMASS_XT30PW-F_1x02_P2.50mm_Horizontal |  | 1
GATE/dVdt | TP4 | TestPoint_Pad_D2.5mm |  | 1
EN/UVLO | TP2 | TestPoint_Pad_D2.5mm |  | 1
~{EN} | TP1 | TestPoint_Pad_D2.5mm |  | 1
XT30PW-F | J5 | AMASS_XT30PW-F_1x02_P2.50mm_Horizontal |  | 1
SM04B-PASS | J9 | JST_PA_SM04B-PASS_1x04_P2.00mm_Horizontal |  | 1

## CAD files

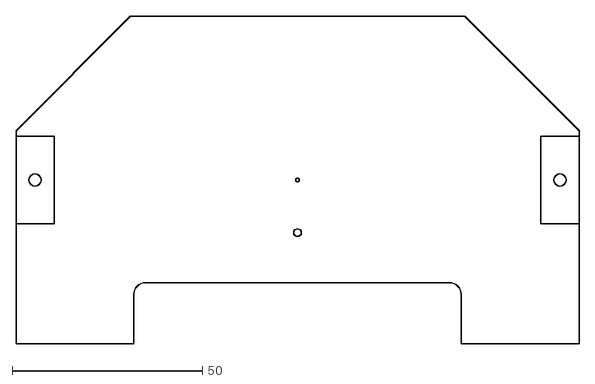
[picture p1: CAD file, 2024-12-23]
robot/control/v3.0/TempControlPCB origin fixed.dxf
148.0 x 86.0

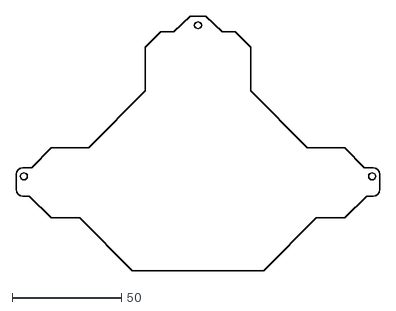
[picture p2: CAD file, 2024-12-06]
robot/kicker/v4.0/TempKickerPCB - TempKickerPCB.dxf
166.0 x 116.0

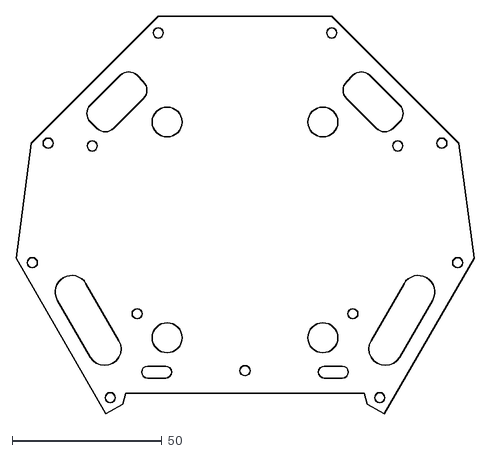
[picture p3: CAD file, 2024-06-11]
robot/midplate/2024/midplate/Plates - Mid Plate.dxf
152.9 x 132.8

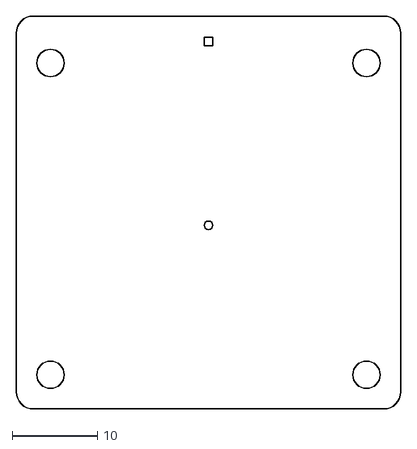
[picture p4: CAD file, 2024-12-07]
robot/motor-controller/v1.1/TempMotorPCB - TempMotorPCB.dxf
45.0 x 46.0

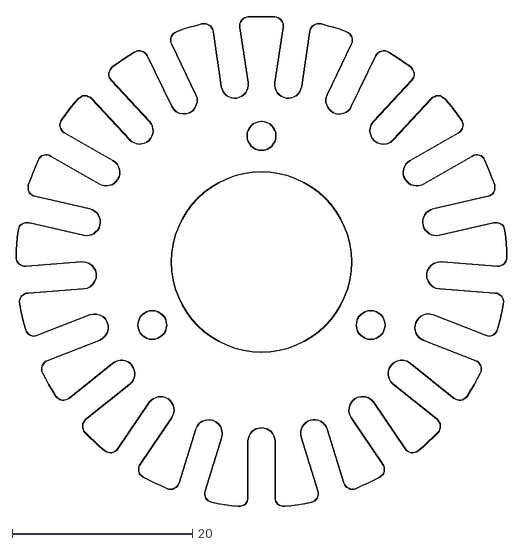
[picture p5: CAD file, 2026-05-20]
robot/omni-wheel-cover/v1.1/omni-wheel-cover/OmniWheel_Cover_v1.1.dxf
54.5 x 54.4

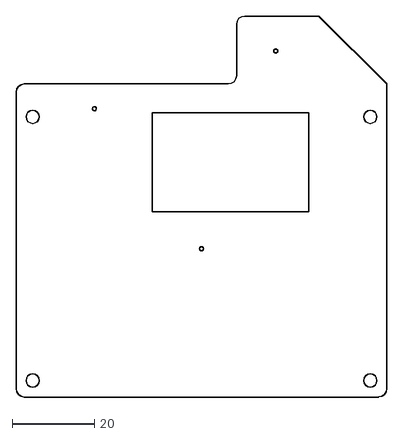
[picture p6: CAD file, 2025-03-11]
robot/power/v1.1/TempPowerPCB - RoundedCorners.dxf
90.0 x 92.5

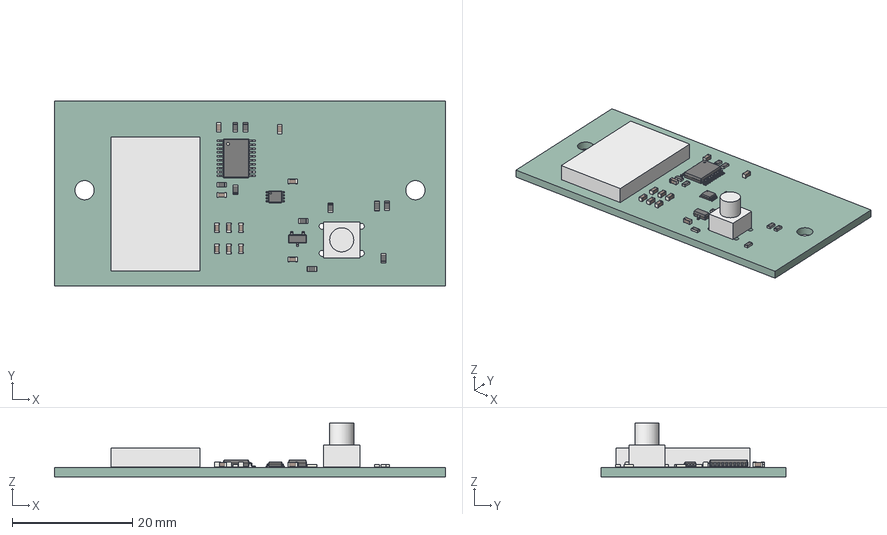
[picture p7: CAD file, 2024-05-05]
robot/radio/v2.0/radio/radio.step
65.0 x 30.8 x 8.93 mm
PCB

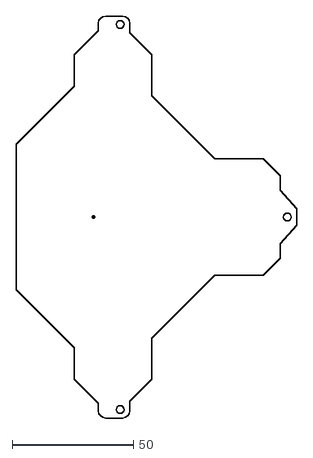
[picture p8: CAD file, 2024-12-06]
robot/kicker/v4.0/TempKickerPCB - TempKickerPCB - WithOriginLocator.dxf
116.0 x 166.0

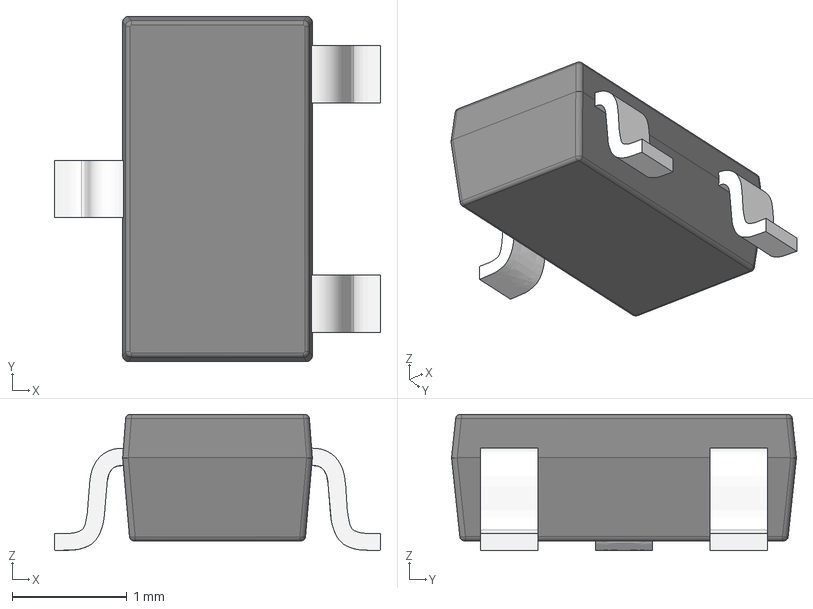
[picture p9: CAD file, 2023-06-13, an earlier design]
robot/breakbeam/v1.2.0/SOT23-3.stp
2.84 x 3.00 x 1.18 mm

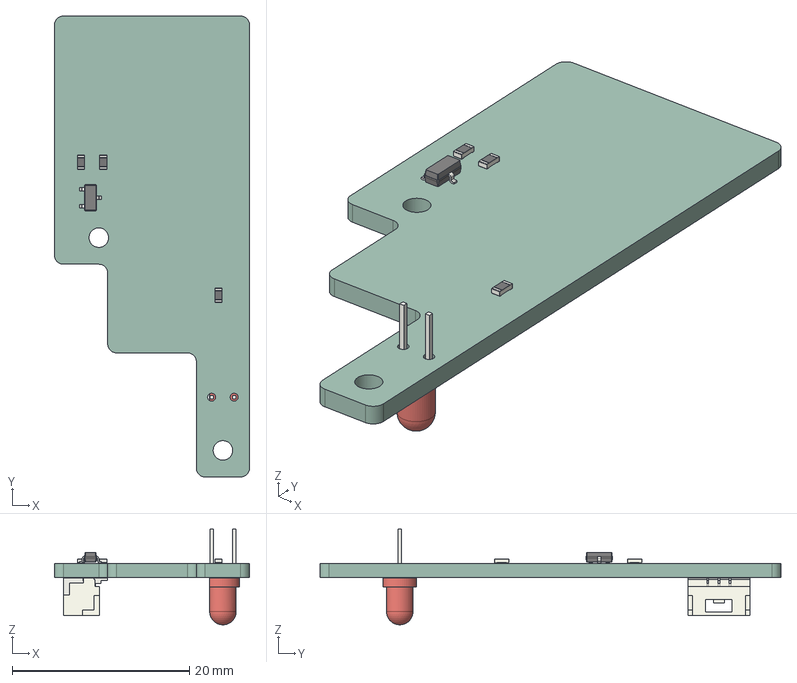
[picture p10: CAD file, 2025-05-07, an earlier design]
robot/breakbeam/v2.0/breakbeam-emitter/breakbeam-emitter.step
22.0 x 52.0 x 10.8 mm
R_0603_1608Metric x 3
SOT_23
JST_SM03B_GHS_TB
LED_D3.0mm
breakbeam-emitter_PCB

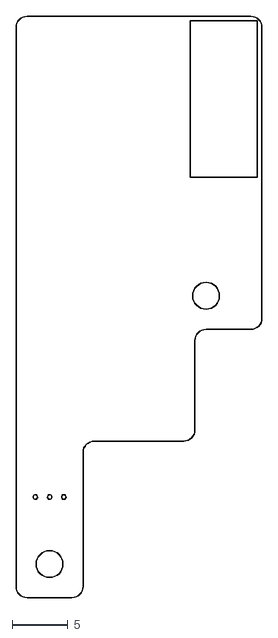
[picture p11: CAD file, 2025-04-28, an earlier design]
robot/breakbeam/v2.0/TempBreakbeamPCB.dxf
22.0 x 52.0

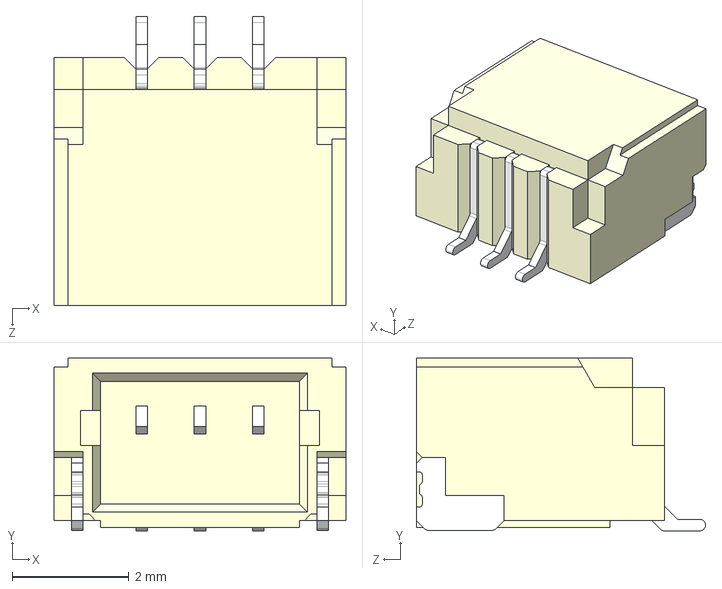
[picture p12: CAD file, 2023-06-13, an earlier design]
robot/breakbeam/v1.2.0/SM03B-SRSS-TB_LF__SN_.step
5.00 x 2.96 x 4.95 mm

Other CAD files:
robot/breakbeam/v2.0/breakbeam-receiver/breakbeam-receiver.step

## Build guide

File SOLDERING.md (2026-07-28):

# A-Team Soldering Guide

During fleet board production, the team soldered many components JLC did not have in stock. These also tended to be the more complex components.

The team noticed that minor soldering technique choices had a substantial impact on reliability and yield rate. Specific materials and techniques that made differences in our success are documented below.

## Solder Choice

Leaded solder should be used (60/40 or 63/37) to reduce the hot air reflow temperature. Especially on larger boards (like control), lower and slower temperature bring ups reduce warping from localized heating. This impacts yield rate of components like the stm32h7 in the large lqfp-144 package that need a highly planer board to adhere all pins.

Keeping the reflow temperature low was also important for our Odin-W262 radio, which is a SoM board made with lead-free solder. Keeping the temperature low means we do not reflow the SoM components when attaching the SoM to our board.

If the team has a bottom heating apparatus, this is much less of a factor.  

## Choice in Flux and Cleaning Agent

The high efficiency switching power supplies were highly sensitive to cleaning method and flux choice, as small leakage currents on voltage and current sense area could produce DC error or instability in the rail.

It is absolutely required that 90-99% IPA be used as the cleaning agent. DO NOT USE 70% IPA. It does not dry sufficiently for a reliable product.

We recommend the use of ChipQuik WS991. We also recommend against using other water soluable variants as we noticed it seemed to bubble up when very low currents passed though it over time. The exact mechnism was unclear. This caused yield rate problems in stspins and U2. 

## Parts with EPAD

For parts with a ground pad underneath, take care not to overfill the pad. When the part is pushed down this can cause shorting to pins underneath. This is easy to do because a larger pad size (EPAD) compared with the other package pins produces a larger meniscus, which is non-linear.

Espcially on switching power supplies with very low resistance current detection, the potential difference created between CSN and EPAD due to a large solder blob on EPAD may be non-trivial. This was the case with the 12V regulator (U2), and the lt3751 and lt3757 on the kicker versions.

## IMUs

The small LGA IMUs are quite difficult to solder. We found yield rates increased by fluxing then tinning both the board *AND* the part, then reflowing the part onto the board.

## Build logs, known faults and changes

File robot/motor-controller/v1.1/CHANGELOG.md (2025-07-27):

# Motor Controller v1.1 Changelog
 - adds independent fusing for stspin Vmotor, provides better isolation if Vmotor bridges to other rails
 - adds TVS diode after 3v3 fuse, provides better isolation in the event Vmotor bridges to 3v3
 - adds low-half resistors to current sense and OCP DC offset circuity, decouples from amp leakage calibration
 - adds current limiting resistor to RST transistor gate

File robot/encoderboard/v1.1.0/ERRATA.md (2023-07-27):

# Errata for Encoderboard v1.1.0

No known issues.

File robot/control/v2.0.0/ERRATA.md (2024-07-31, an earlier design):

# Control v2.0 Errata

 - KICKER_DET line is not actually routed to the MCU. Detection implemented using other means in firmware
 - LT4367 protection chip still does not full survive repeated battery hot plug events. Can be bypassed by depopulating R7, R8, R9, and R10 and then solder bridging U2.1 with U2.2 and U2.3 with U3.4, disabling UV and OV protections. 
 - stspin motor controller watchdog protections do not work because nrst is driven high with a Lo-Z source by the MCU. Depopulate R91, R121, R151, R181, R211 and load the latest comp firmware. 
 - depopulate R14, pull up technically overvolts downstream regulator enable pin but current is VERY low

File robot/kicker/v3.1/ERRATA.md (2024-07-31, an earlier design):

# Kicker v3.1 Errata

 - boot1 is not pulled down, fix by connecting J16.3 to J16.1 with a 10k ohm resistor

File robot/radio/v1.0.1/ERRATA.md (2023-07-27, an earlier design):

# Errata for Radio v1.1.0

No known issues.

Notes: if you want flow control enabled, bridge OPPOSITE corner jumpers. CTS->RTS, RTS->CTS

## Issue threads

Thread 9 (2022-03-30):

Bodge Bot Power Supply

gtrosawa, 2022-03-30:

Closed 2024-04-28.

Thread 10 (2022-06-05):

Investigate SD vs eMMC

guyfleeman, 2022-06-05:
SD cheaper, removable

eMMC more robust against vibration/impact

guyfleeman, 2022-07-13:
going with SD for now. Firmware effort required to support eMMC (e.g. writing USB passthru to mount robot as blk storage device) is too high for now

Closed 2022-07-13.

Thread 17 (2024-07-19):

Add very high impedance pull-ups on UART to handle reset noise

joe-spall, 2024-07-19:

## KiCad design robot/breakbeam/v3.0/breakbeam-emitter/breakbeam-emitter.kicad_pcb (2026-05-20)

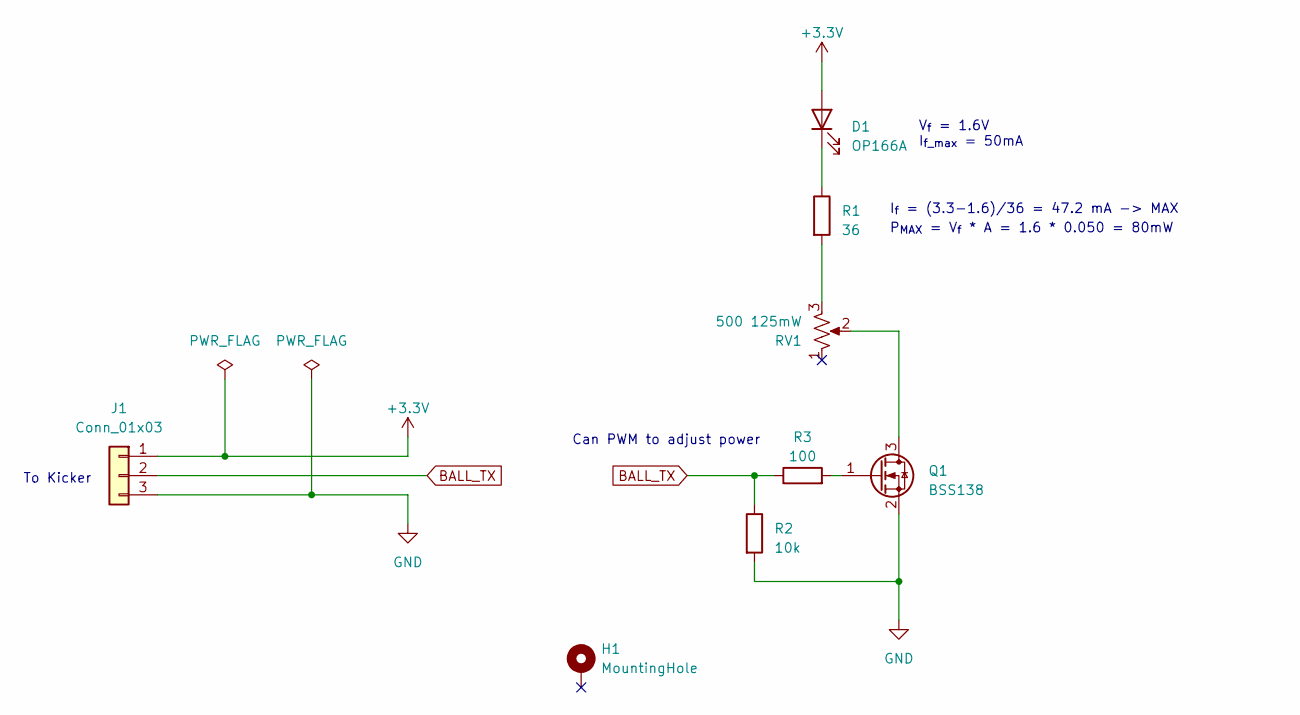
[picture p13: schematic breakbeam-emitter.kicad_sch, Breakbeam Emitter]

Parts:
D1: OP166A; LED_D3.0mm
H1: MountingHole; MountingHole_3.2mm_M3_ISO7380_Pad
J1: Conn_01x03; JST_SH_SM03B-SRSS-TB_1x03-1MP_P1.00mm_Horizontal; LCSC C160403
Q1: BSS138; SOT-23; LCSC C82045
R1: 36; R_0603_1608Metric_Pad0.98x0.95mm_HandSolder; LCSC C101000
R2: 10k; R_0603_1608Metric_Pad0.98x0.95mm_HandSolder; LCSC C25804
R3: 100; R_0603_1608Metric_Pad0.98x0.95mm_HandSolder; LCSC C22775
RV1: 500 125mW; Potentiometer_Bourns_TC33X_Vertical; LCSC C720649

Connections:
+3.3V: D1.2 (A), J1.1
BALL_TX: J1.2, R2.1, R3.1
GND: J1.3, Q1.2 (S), R2.2
unnamed: D1.1 (K), R1.1
unnamed: Q1.3 (D), RV1.2
unnamed: Q1.1 (G), R3.2
unnamed: R1.2, RV1.3

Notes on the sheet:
P_{MAX} = V_{f} * A = 1.6 * 0.050 = 80mW
I_{f} = (3.3-1.6)/36 = 47.2 mA -> MAX
To Kicker
V_{f} = 1.6V I_{f_max} = 50mA
Can PWM to adjust power

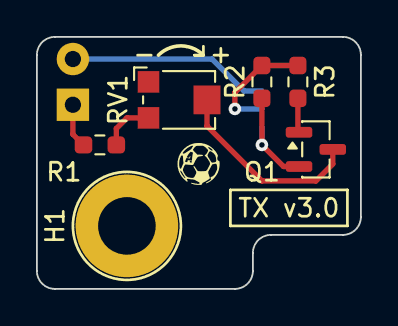
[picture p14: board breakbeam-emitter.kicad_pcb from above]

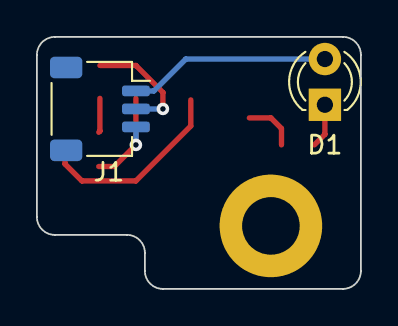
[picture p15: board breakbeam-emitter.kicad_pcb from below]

Board: 2 copper layers, 18.0 x 14.0 mm, 8 parts (2 on the bottom side), 7 nets.

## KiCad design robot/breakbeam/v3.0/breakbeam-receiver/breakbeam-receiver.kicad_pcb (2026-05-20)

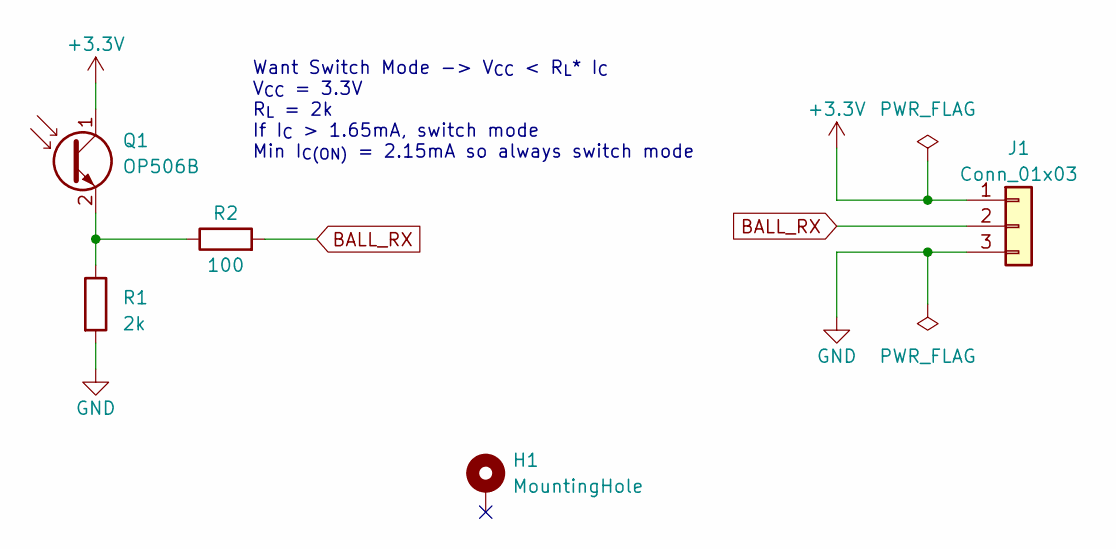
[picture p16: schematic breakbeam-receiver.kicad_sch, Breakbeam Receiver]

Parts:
H1: MountingHole; MountingHole_3.2mm_M3_ISO7380_Pad
J1: Conn_01x03; JST_SH_SM03B-SRSS-TB_1x03-1MP_P1.00mm_Horizontal; LCSC C160403
Q1: OP506B; LED_D3.0mm
R1: 2k; R_0603_1608Metric; LCSC C22975
R2: 100; R_0603_1608Metric; LCSC C22775

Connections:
+3.3V: J1.1, Q1.1 (C)
BALL_RX: J1.2, R2.2
GND: J1.3, R1.2
unnamed: Q1.2 (E), R1.1, R2.1

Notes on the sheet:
Want Switch Mode -> V_{CC} < R_{L}* I_{C} V_{CC} = 3.3V R_{L} = 2k If I_{C} > 1.65mA, switch mode Min I_{C(ON)} = 2.15mA so always switch mode

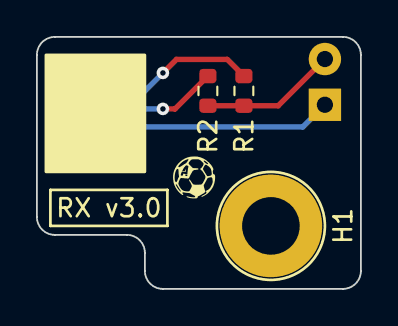
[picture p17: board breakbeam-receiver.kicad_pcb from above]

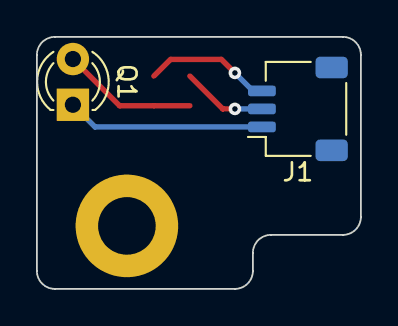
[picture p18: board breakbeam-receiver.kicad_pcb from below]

Board: 2 copper layers, 18.0 x 14.0 mm, 5 parts (2 on the bottom side), 4 nets.

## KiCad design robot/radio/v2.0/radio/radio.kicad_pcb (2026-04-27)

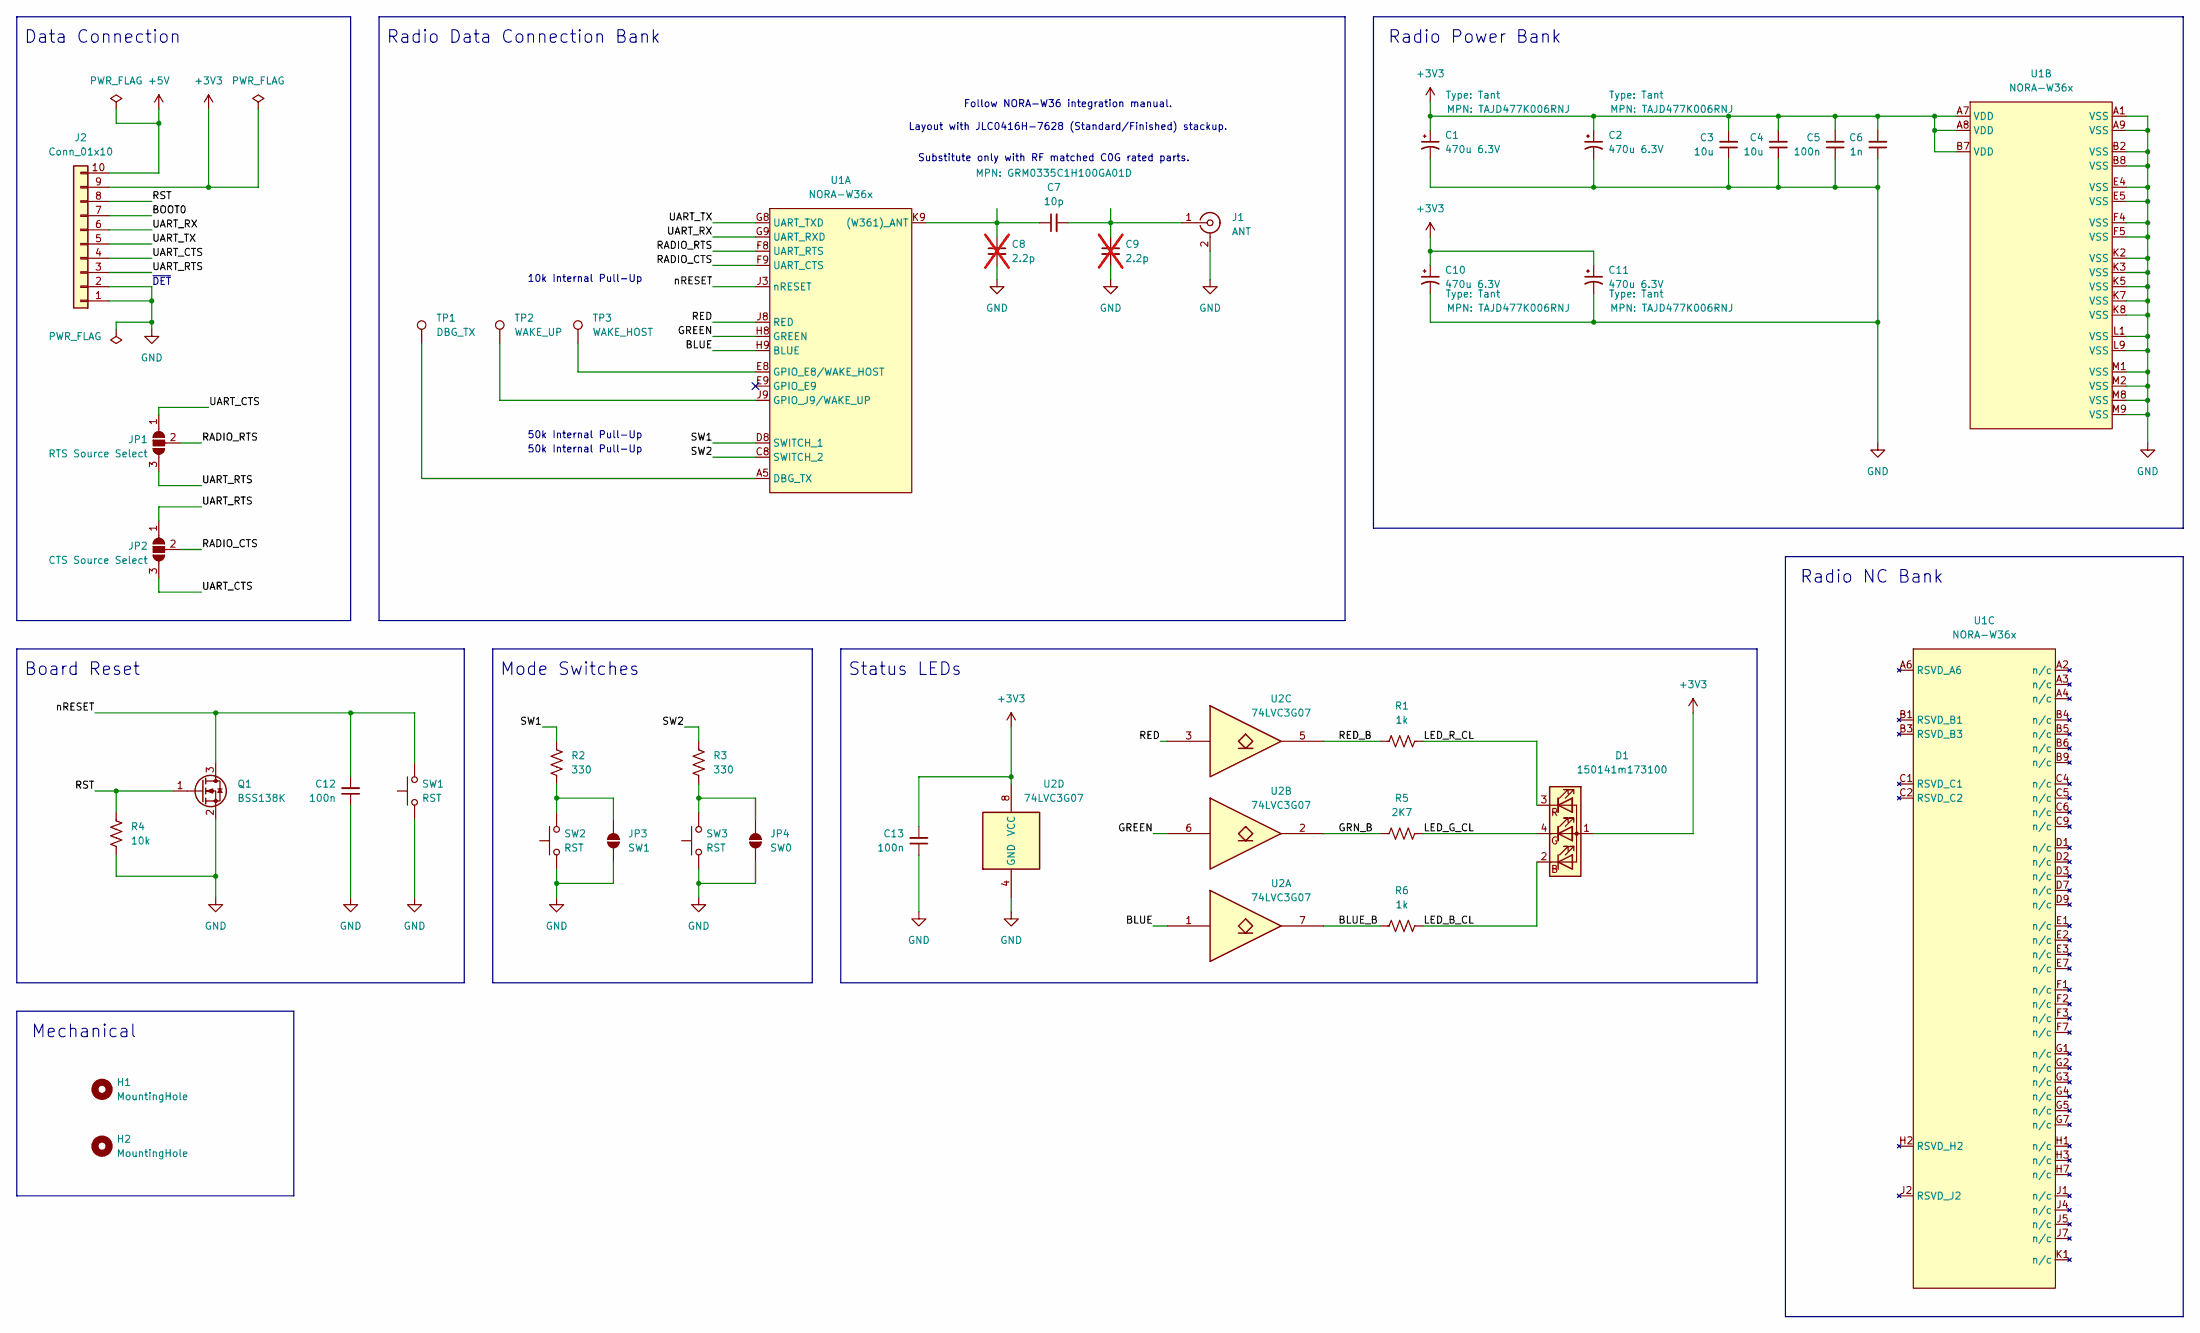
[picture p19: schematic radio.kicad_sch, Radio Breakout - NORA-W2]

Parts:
C1, C2, C10, C11: 470u 6.3V; CP_EIA-7343-31_Kemet-D_HandSolder; MPN TAJD477K006RNJ; LCSC C7229
C3, C4: 10u; C_0603_1608Metric; LCSC C96446
C5, C12, C13: 100n; C_0603_1608Metric; LCSC C14663
C6: 1n; C_0603_1608Metric; LCSC C100040
C7: 10p; C_0201_0603Metric; MPN GRM0335C1H100GA01D; LCSC C384956
C8, C9: 2.2p; C_0201_0603Metric; not fitted
D1: 150141m173100; LED_RGB_Wuerth-PLCC4_3.2x2.8mm_150141M173100; LCSC C5342281
H1, H2: MountingHole; MountingHole_3.2mm_M3
J1: ANT; U.FL_Hirose_U.FL-R-SMT-1_Vertical; LCSC C88374
J2: Conn_01x10; JST_SH_SM10B-SRSS-TB_1x10-1MP_P1.00mm_Horizontal; LCSC C160409
JP1: RTS Source Select; SolderJumper-3_P1.3mm_Bridged12_RoundedPad1.0x1.5mm_NumberL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
JP2: CTS Source Select; SolderJumper-3_P1.3mm_Bridged12_RoundedPad1.0x1.5mm_NumberL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
JP3: SW1; SolderJumper-2_2.0x1.2mm_Open
JP4: SW0; SolderJumper-2_2.0x1.2mm_Open
Q1: BSS138K; SOT-23; LCSC C255592
R1, R6: 1k; R_0603_1608Metric; LCSC C21190
R2, R3: 330; R_0603_1608Metric
R4: 10k; R_0603_1608Metric
R5: 2K7; R_0603_1608Metric
SW1, SW2, SW3: RST; SW_SPST_TL3305A; LCSC C2886902
TP1: DBG_TX; TestPoint_Pad_D1.5mm
TP2: WAKE_UP; TestPoint_Pad_D1.5mm
TP3: WAKE_HOST; TestPoint_Pad_D1.5mm
U1: NORA-W36x; NORA_W366
U2: 74LVC3G07; VSSOP-8_2.3x2mm_P0.5mm; LCSC C548751

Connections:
+3V3: C1.1, C2.1, C3.2, C4.2, C5.2, C6.2, C10.1, C11.1, C13.2, D1.1 (A), J2.9, U1.A7 (VDD), U1.A8 (VDD), U1.B7 (VDD), U2.8 (VCC)
+5V: J2.10
/BLUE: U1.H9 (BLUE), U2.1
/BLUE_B: R6.1, U2.7
/BOOT0: J2.7
/GREEN: U1.H8 (GREEN), U2.6
/GRN_B: R5.1, U2.2
/LED_B_CL: D1.2 (BK), R6.2
/LED_G_CL: D1.4 (GK), R5.2
/LED_R_CL: D1.3 (RK), R1.2
/RADIO_CTS: JP2.2 (C), U1.F9 (UART_CTS)
/RADIO_RTS: JP1.2 (C), U1.F8 (UART_RTS)
/RED: U1.J8 (RED), U2.3
/RED_B: R1.1, U2.5
/RST: J2.8, Q1.1 (G), R4.2
/SW1: R2.2, U1.D8 (SWITCH_1)
/SW2: R3.1, U1.C8 (SWITCH_2)
/UART_CTS: J2.4, JP1.1 (A), JP2.3 (B)
/UART_RTS: J2.3, JP1.3 (B), JP2.1 (A)
/UART_RX: J2.6, U1.G9 (UART_RXD)
/UART_TX: J2.5, U1.G8 (UART_TXD)
/nRESET: C12.2, Q1.3 (D), SW1.2, U1.J3 (nRESET)
GND: C1.2, C2.2, C3.1, C4.1, C5.1, C6.1, C8.2, C9.2, C10.2, C11.2, C12.1, C13.1, J1.2 (Ext), J2.1, J2.2, JP3.1 (A), JP4.1 (A), Q1.2 (S), R4.1, SW1.1, SW2.1, SW3.1, U1.A1 (VSS), U1.A9 (VSS), U1.B2 (VSS), U1.B8 (VSS), U1.E4 (VSS), U1.E5 (VSS), U1.F4 (VSS), U1.F5 (VSS), U1.K2 (VSS), U1.K3 (VSS), U1.K5 (VSS), U1.K7 (VSS), U1.K8 (VSS), U1.L1 (VSS), U1.L9 (VSS), U1.M1 (VSS), U1.M2 (VSS), U1.M8 (VSS), U1.M9 (VSS), U2.4 (GND)
unnamed: C7.2, C9.1, J1.1 (In)
unnamed: JP3.2 (B), R2.1, SW2.2
unnamed: JP4.2 (B), R3.2, SW3.2
unnamed: C7.1, C8.1, U1.K9 ((W361)_ANT)
unnamed: TP1.1, U1.A5 (DBG_TX)
unnamed: TP3.1, U1.E8 (GPIO_E8/WAKE_HOST)
unnamed: TP2.1, U1.J9 (GPIO_J9/WAKE_UP)

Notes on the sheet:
Radio Power Bank
50k Internal Pull-Up
Radio Data Connection Bank
Follow NORA-W36 integration manual. Layout with JLC0416H-7628 (Standard/Finished) stackup.
~{DET}
Data Connection
10k Internal Pull-Up
Board Reset
Status LEDs
Substitute only with RF matched C0G rated parts.
Mode Switches
Radio NC Bank
Mechanical

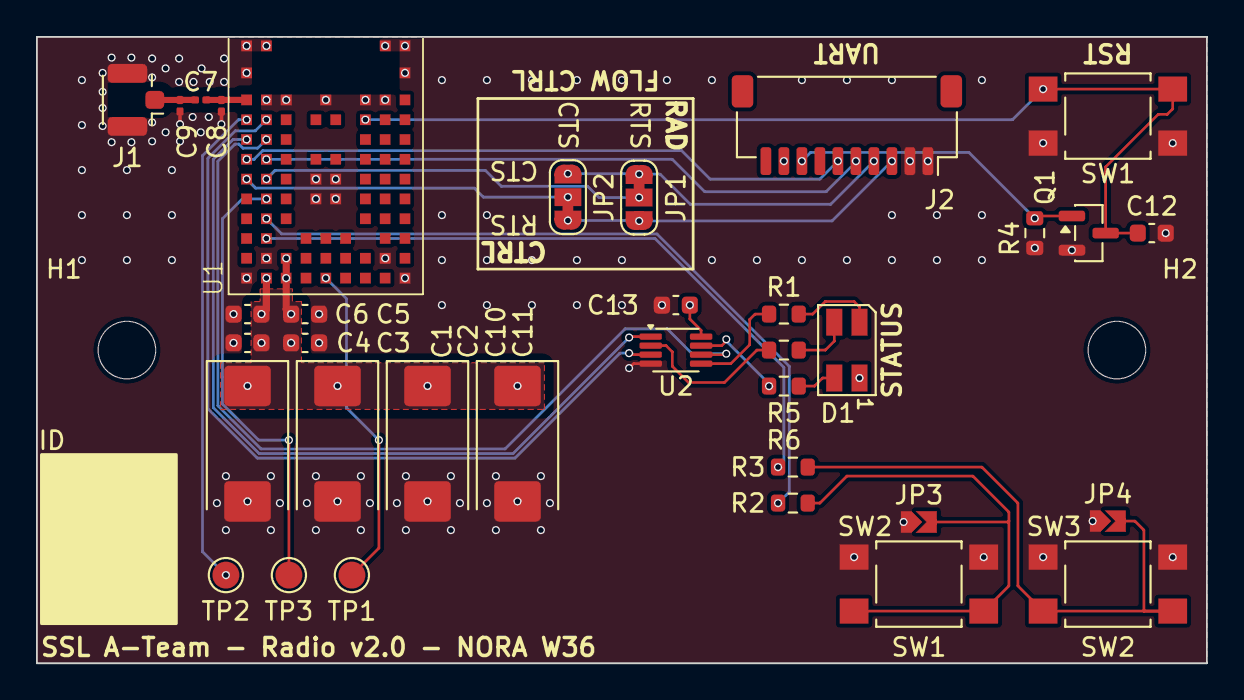
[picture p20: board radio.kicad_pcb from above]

Board: 4 copper layers, 65.0 x 34.8 mm, 37 parts (0 on the bottom side), 28 nets.

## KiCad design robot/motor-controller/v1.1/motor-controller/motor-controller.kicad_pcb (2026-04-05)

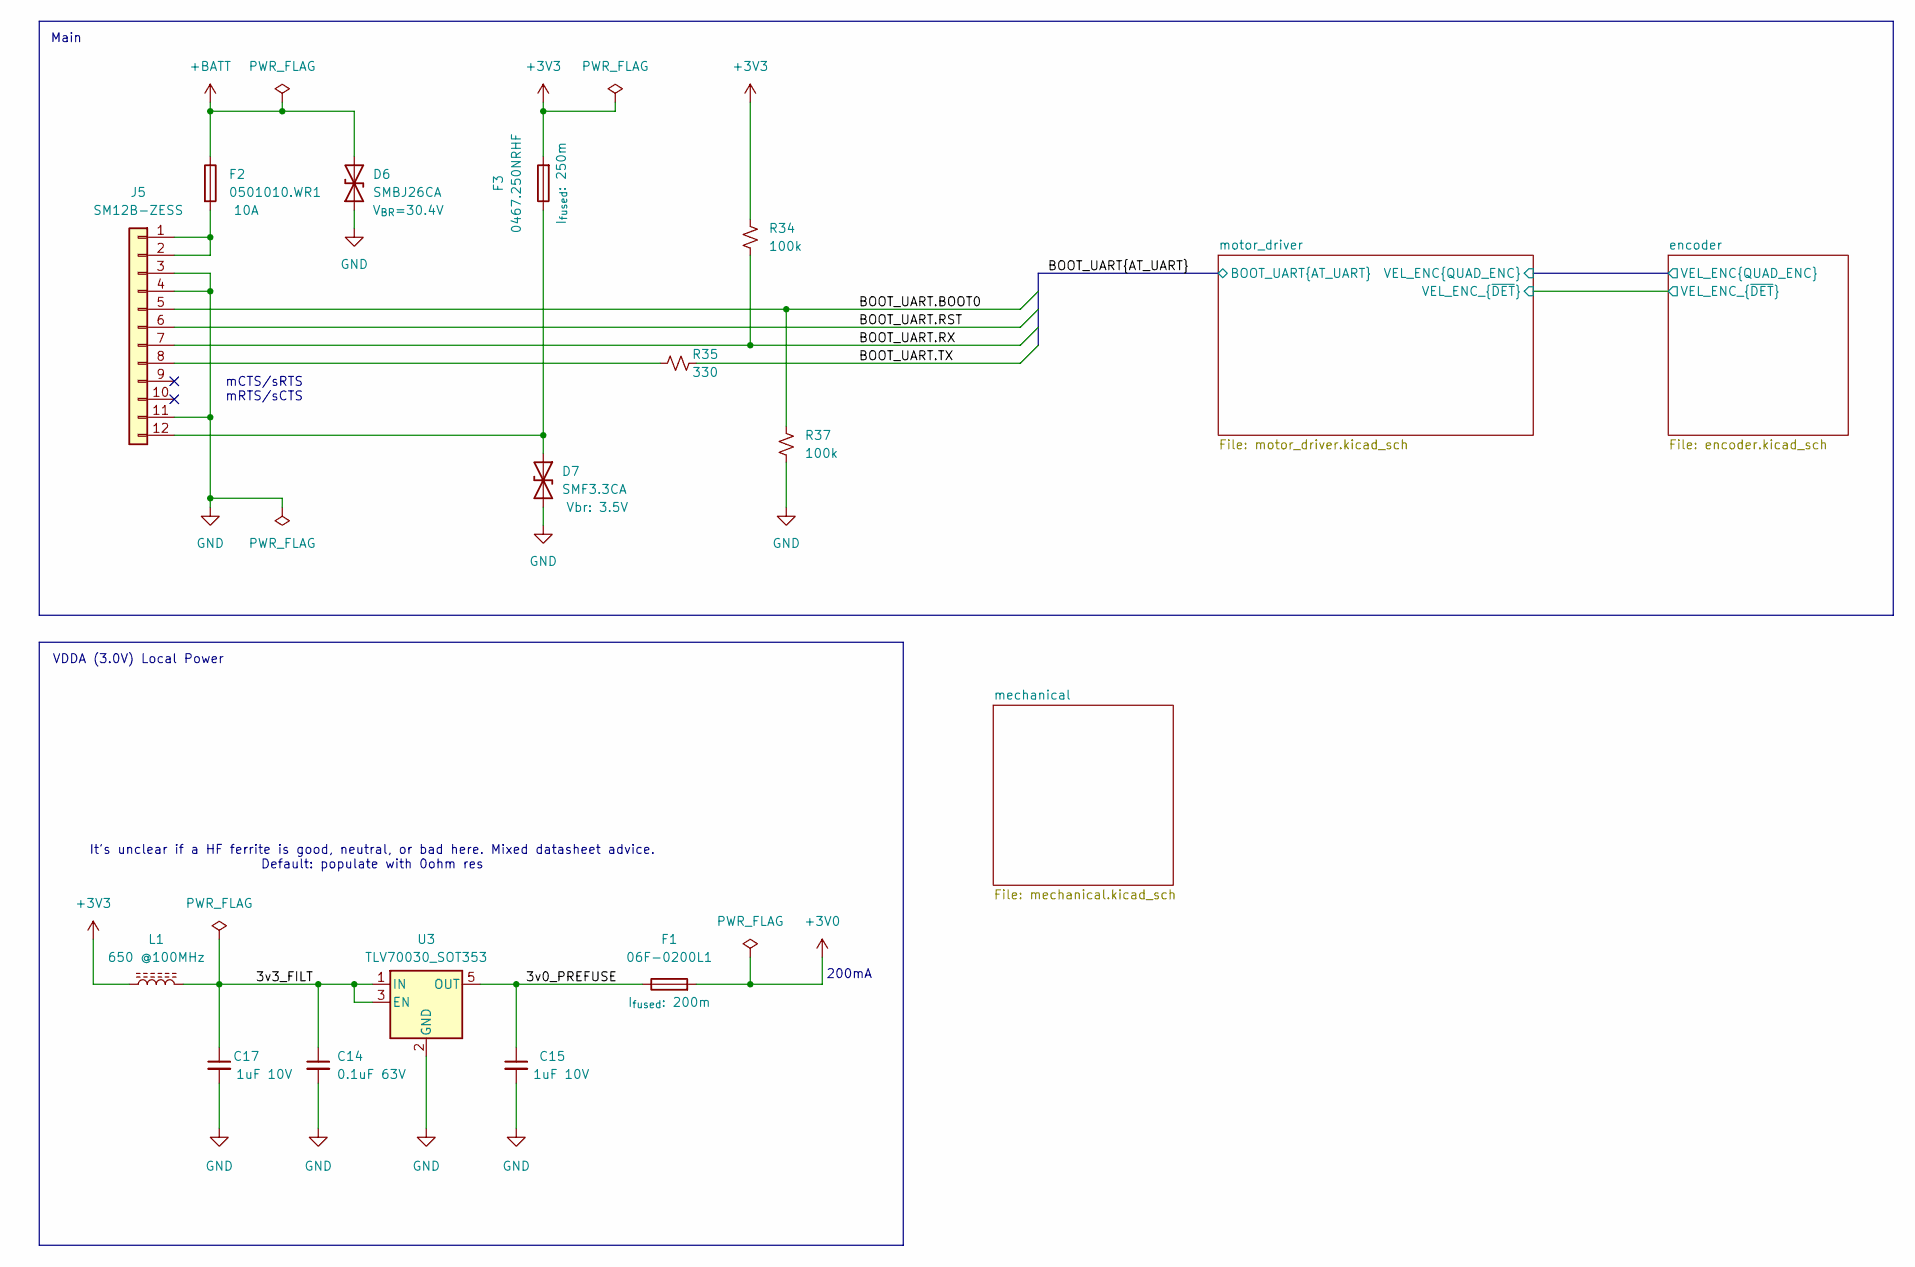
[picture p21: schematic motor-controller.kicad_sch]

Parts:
C14: 0.1uF 63V; C_0402_1005Metric; LCSC C131394
C15, C17: 1uF 10V; C_0402_1005Metric; LCSC C14445
D6: SMBJ26CA; D_SMB_Non-Polar; LCSC C135063
D7: SMF3.3CA; D_SOD-123; LCSC C6165153
F1: 06F-0200L1; Fuse_0603_1608Metric_Pad1.05x0.95mm_HandSolder; LCSC C377220
F2: 0501010.WR1; Fuse_1206_3216Metric_Pad1.42x1.75mm_HandSolder; LCSC C207003
F3: 0467.250NRHF; Fuse_0603_1608Metric_Pad1.05x0.95mm_HandSolder; LCSC C151137
J5: SM12B-ZESS; JST_ZE_SM12B-ZESS-TB_1x12-1MP_P1.50mm_Horizontal
L1: 650 @100MHz; R_0603_1608Metric; LCSC C21189
R34, R37: 100k; R_0402_1005Metric; LCSC C25741
R35: 330; R_0402_1005Metric; LCSC C25104
U3: TLV70030_SOT353; SOT-353_SC-70-5; LCSC C527437

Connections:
+3V0: F1.2; also elsewhere on the board
+3V3: F3.2, L1.1, R34.1; also elsewhere on the board
+BATT: D6.2 (A2), F2.1; also elsewhere on the board
/3v0_PREFUSE: C15.1, F1.1, U3.5 (OUT)
/3v3_FILT: C14.1, C17.1, L1.2, U3.1 (IN), U3.3 (EN)
/BOOT_UART.BOOT0: J5.5, R37.1; also elsewhere on the board
/BOOT_UART.RST: J5.6; also elsewhere on the board
/BOOT_UART.RX: J5.7, R34.2; also elsewhere on the board
/BOOT_UART.TX: R35.2; also elsewhere on the board
GND: C14.2, C15.2, C17.2, D6.1 (A1), D7.2 (A2), J5.3, J5.4, J5.11, R37.2, U3.2 (GND); also elsewhere on the board
unnamed: D7.1 (A1), F3.1, J5.12
unnamed: F2.2, J5.1, J5.2
unnamed: J5.8, R35.1

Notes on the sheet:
VDDA (3.0V) Local Power
It's unclear if a HF ferrite is good, neutral, or bad here. Mixed datasheet advice. Default: populate with 0ohm res
Main
200mA
mCTS/sRTS mRTS/sCTS

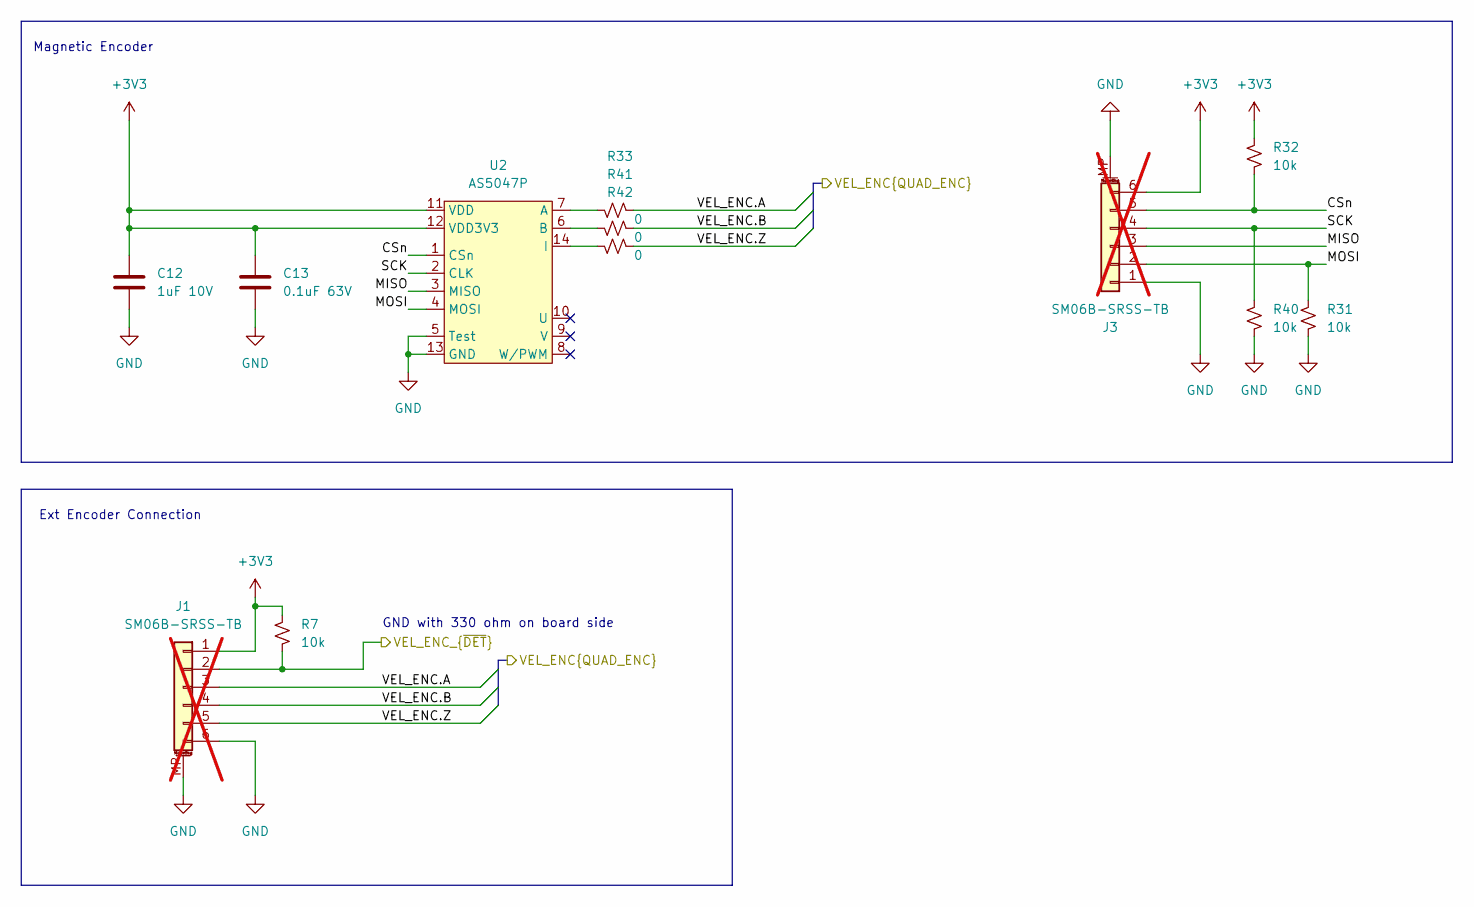
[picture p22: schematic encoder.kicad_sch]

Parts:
C12: 1uF 10V; C_0402_1005Metric; LCSC C14445
C13: 0.1uF 63V; C_0402_1005Metric; LCSC C131394
J1, J3: SM06B-SRSS-TB; JST_SH_SM06B-SRSS-TB_1x06-1MP_P1.00mm_Horizontal; LCSC C160405; not fitted
R7, R31, R32, R40: 10k; R_0402_1005Metric; LCSC C60490
R33, R41, R42: 0; R_0402_1005Metric; LCSC C17168
U2: AS5047P; TSSOP-14_4.4x5mm_P0.65mm; LCSC C962063

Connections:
+3V3: C12.1, C13.1, J1.1, J3.6, R7.2, R32.2, U2.11 (VDD), U2.12 (VDD3V3); also elsewhere on the board
/encoder/CSn: J3.5, R32.1, U2.1 (CSn)
/encoder/MISO: J3.3, U2.3 (MISO)
/encoder/MOSI: J3.2, R31.2, U2.4 (MOSI)
/encoder/SCK: J3.4, R40.2, U2.2 (CLK)
/encoder/VEL_ENC.A: J1.3, R33.1; also elsewhere on the board
/encoder/VEL_ENC.B: J1.4, R41.1; also elsewhere on the board
/encoder/VEL_ENC.Z: J1.5, R42.1; also elsewhere on the board
/motor_driver/VEL_ENC_{~DET}: J1.2, R7.1; also elsewhere on the board
GND: C12.2, C13.2, J1.6, J1.MP (MountPin), J3.1, J3.MP (MountPin), R31.1, R40.1, U2.5 (Test), U2.13 (GND); also elsewhere on the board
unnamed: R33.2, U2.7 (A)
unnamed: R41.2, U2.6 (B)
unnamed: R42.2, U2.14 (I)

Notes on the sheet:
Ext Encoder Connection
Magnetic Encoder
GND with 330 ohm on board side

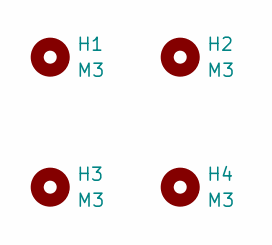
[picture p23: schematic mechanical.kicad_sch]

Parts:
H1, H2, H3, H4: M3; MountingHole_3.2mm_M3_Pad_TopBottom

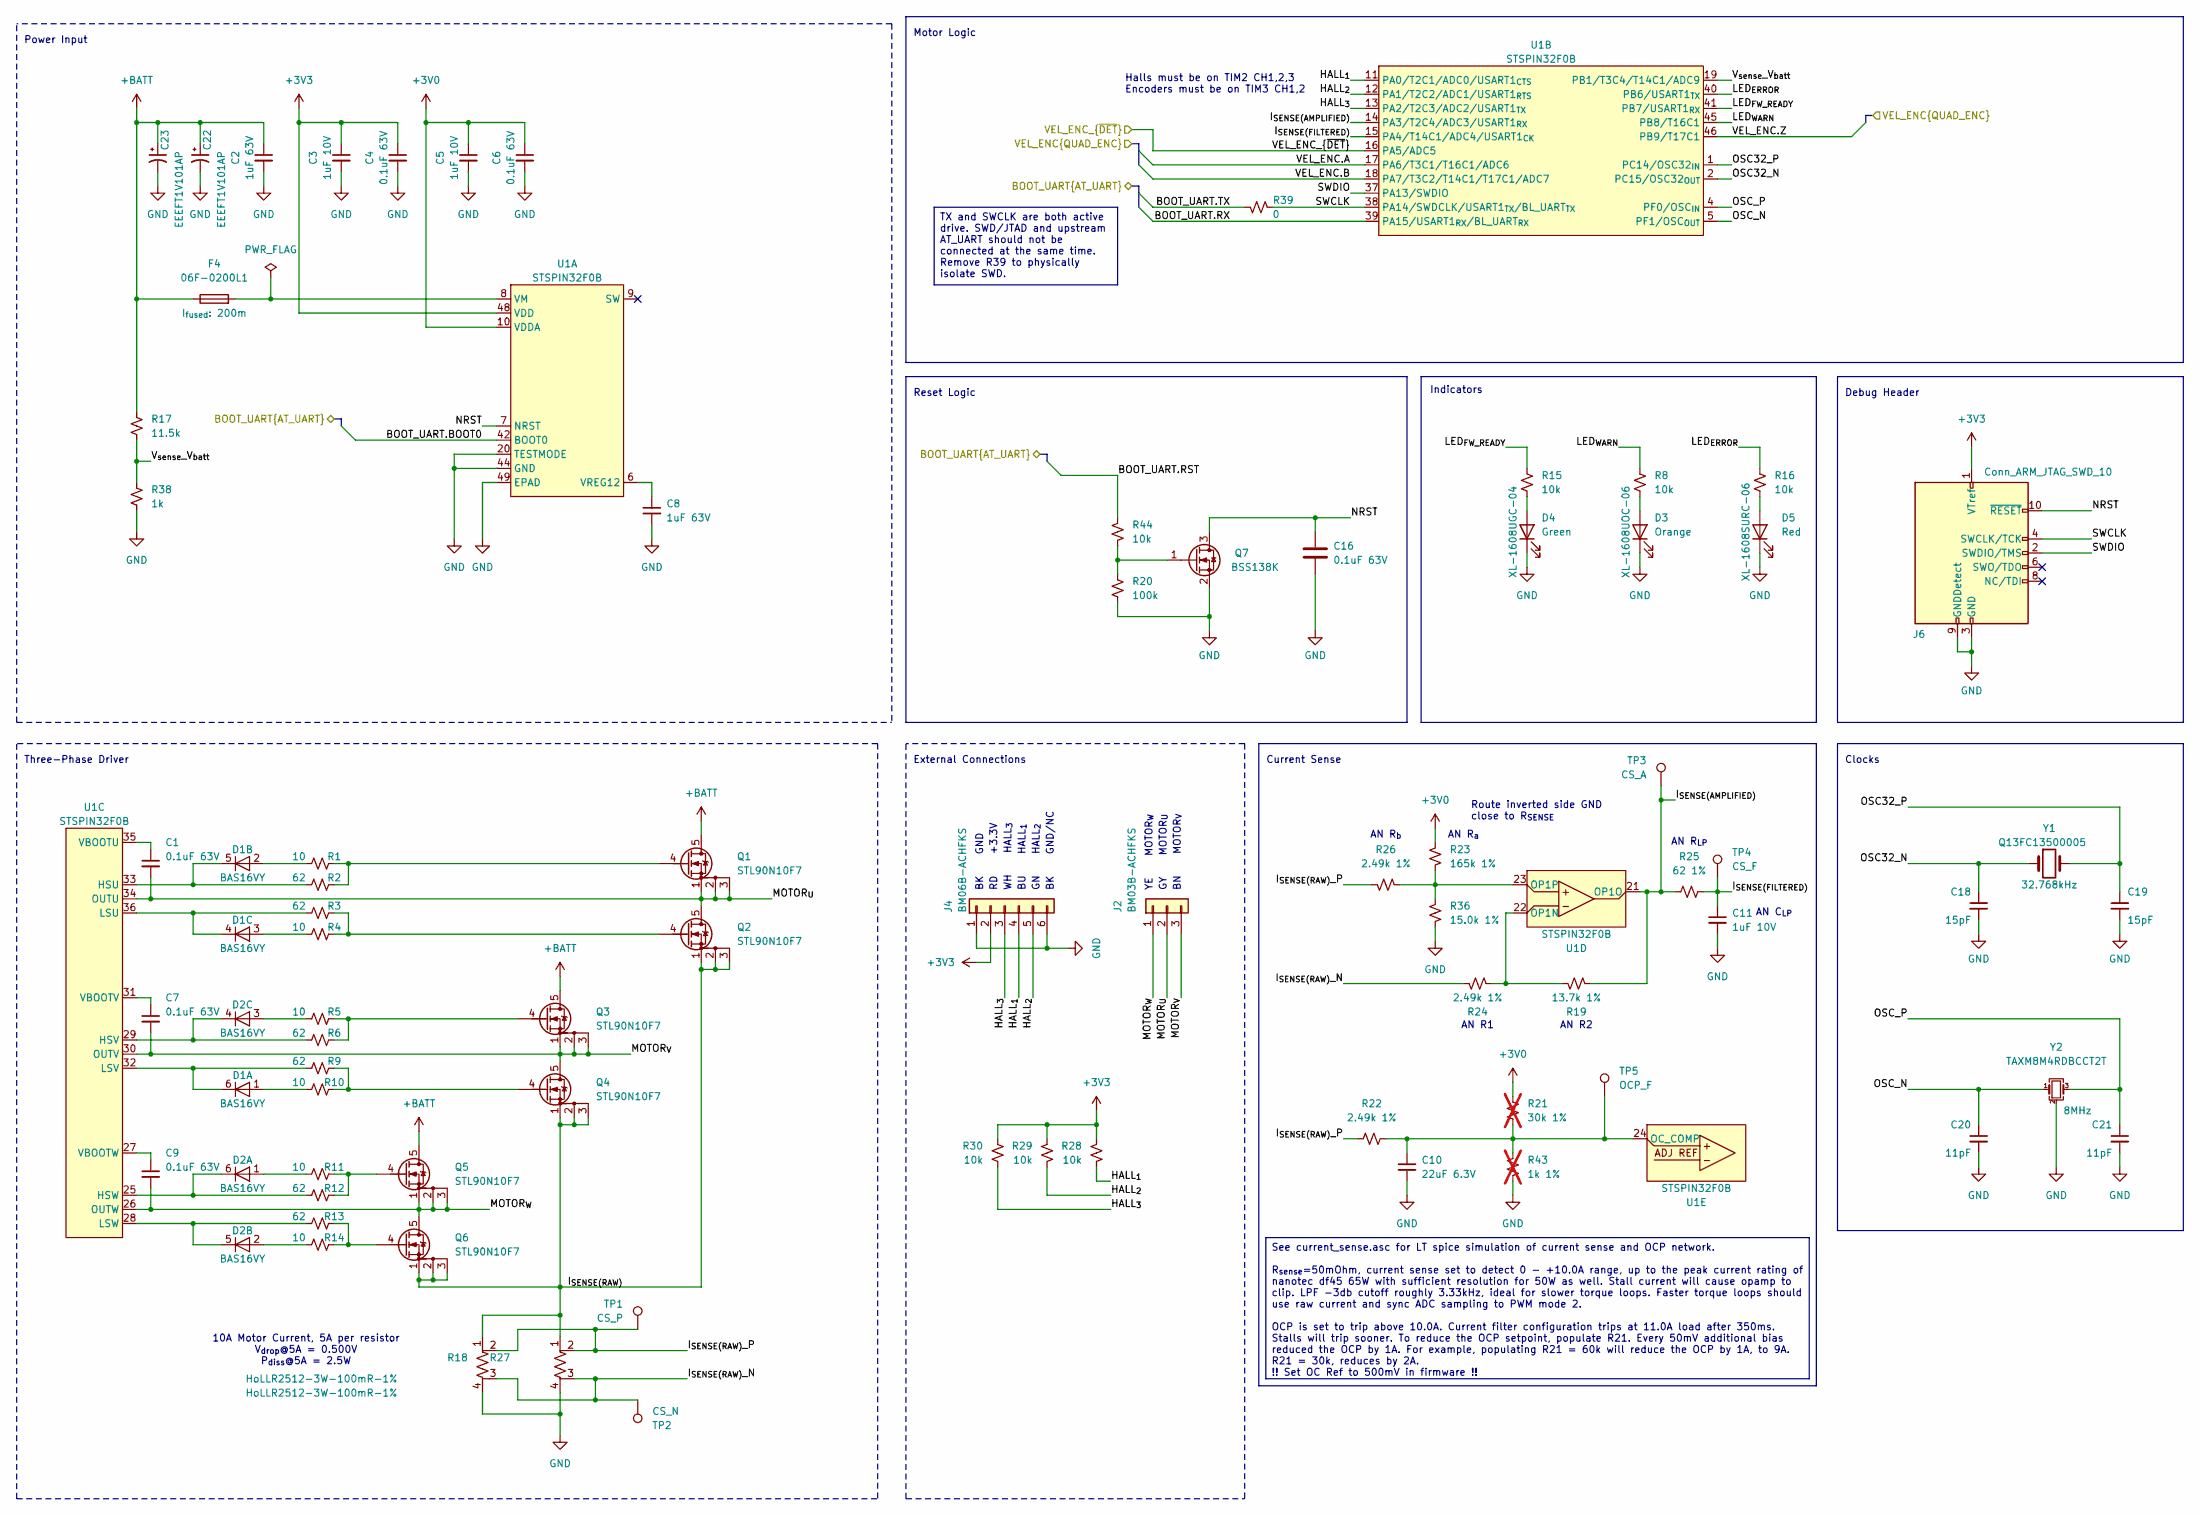
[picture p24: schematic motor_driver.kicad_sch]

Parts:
C1, C4, C6, C7, C9, C16: 0.1uF 63V; C_0402_1005Metric; LCSC C131394
C2, C8: 1uF 63V; C_1206_3216Metric; LCSC C70463
C3, C5, C11: 1uF 10V; C_0402_1005Metric; LCSC C14445
C10: 22uF 6.3V; C_0402_1005Metric; LCSC C415703
C18, C19: 15pF; C_0402_1005Metric; LCSC C86285
C20, C21: 11pF; C_0402_1005Metric; LCSC C161525
C22, C23: EEEFT1V101AP; CP_Elec_6.3x5.8; LCSC C128464
D1, D2: BAS16VY; SOT-363_SC-70-6; LCSC C135826
D3: XL-1608UOC-06; LED0603; LCSC C965800
D4: XL-1608UGC-04; LED0603; LCSC C965804
D5: XL-1608SURC-06; LED0603; LCSC C965799
F4: 06F-0200L1; Fuse_0603_1608Metric_Pad1.05x0.95mm_HandSolder; LCSC C377220
J2: BM03B-ACHFKS; JST_ACHFR_03V; LCSC C5177195
J4: BM06B-ACHFKS; JST_ACHFR_06V; LCSC C5304907
J6: Conn_ARM_JTAG_SWD_10; Samtec-2x5pin-1.27mm; LCSC C448647
Q1, Q2, Q3, Q4, Q5, Q6: STL90N10F7; PowerFLAT_5x6; LCSC C457493
Q7: BSS138K; SOT-23; LCSC C5224263
R1, R4, R5, R10, R11, R14: 10; R_0402_1005Metric; LCSC C25077
R2, R3, R6, R9, R12, R13: 62; R_0402_1005Metric; LCSC C100501
R8, R15, R16, R28, R29, R30, R44: 10k; R_0402_1005Metric; LCSC C60490
R17: 11.5k; R_0402_1005Metric; LCSC C270653
R18, R27: HoLLR2512-3W-100mR-1%; 2512_CS_ADI-TypeC; LCSC C2994646
R19: 13.7k 1%; R_0402_1005Metric; LCSC C852522
R20: 100k; R_0402_1005Metric; LCSC C25741
R21: 30k 1%; R_0402_1005Metric; LCSC C25776; not fitted
R22, R24, R26: 2.49k 1%; R_0402_1005Metric; LCSC C852700
R23: 165k 1%; R_0402_1005Metric; LCSC C1509613
R25: 62 1%; R_0402_1005Metric; LCSC C852875
R36: 15.0k 1%; R_0402_1005Metric; LCSC C853539
R38: 1k; R_0402_1005Metric; LCSC C11702
R39: 0; R_0402_1005Metric; LCSC C17168
R43: 1k 1%; R_0402_1005Metric; LCSC C11702; not fitted
TP1: CS_P; TestPoint_Pad_D1.5mm
TP2: CS_N; TestPoint_Pad_D1.5mm
TP3: CS_A; TestPoint_Pad_D1.5mm
TP4: CS_F; TestPoint_Pad_D1.5mm
TP5: OCP_F; TestPoint_Pad_D1.5mm
U1: STSPIN32F0B; QFN-48-1EP_7x7mm_P0.5mm_EP2.8x2.8mm; LCSC C1521053
Y1: Q13FC13500005; Crystal_SMD_3215-2Pin_3.2x1.5mm; LCSC C841881
Y2: TAXM8M4RDBCCT2T; Crystal_SMD_3225-4Pin_3.2x2.5mm; LCSC C400090

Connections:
+3V0: C5.1, C6.1, R21.1, R23.1, U1.10 (VDDA); also elsewhere on the board
+3V3: C3.1, C4.1, J4.2, J6.1 (VTref), R28.1, R29.1, R30.1, U1.48 (VDD); also elsewhere on the board
+BATT: C2.1, C22.1, C23.1, F4.1, Q1.5 (D), Q3.5 (D), Q5.5 (D), R17.1; also elsewhere on the board
/BOOT_UART.BOOT0: U1.42 (BOOT0); also elsewhere on the board
/BOOT_UART.RST: R44.1; also elsewhere on the board
/BOOT_UART.RX: U1.39 (PA15/USART1_{RX}/BL_UART_{RX}); also elsewhere on the board
/BOOT_UART.TX: R39.1; also elsewhere on the board
/encoder/VEL_ENC.A: U1.17 (PA6/T3C1/T16C1/ADC6); also elsewhere on the board
/encoder/VEL_ENC.B: U1.18 (PA7/T3C2/T14C1/T17C1/ADC7); also elsewhere on the board
/encoder/VEL_ENC.Z: U1.46 (PB9/T17C1); also elsewhere on the board
/motor_driver/HALL_{1}: J4.4, R28.2, U1.11 (PA0/T2C1/ADC0/USART1_{CTS})
/motor_driver/HALL_{2}: J4.5, R29.2, U1.12 (PA1/T2C2/ADC1/USART1_{RTS})
/motor_driver/HALL_{3}: J4.3, R30.2, U1.13 (PA2/T2C3/ADC2/USART1_{TX})
/motor_driver/I_{SENSE(AMPLIFIED)}: R19.2, R25.1, TP3.1, U1.14 (PA3/T2C4/ADC3/USART1_{RX}), U1.21 (OP1O)
/motor_driver/I_{SENSE(FILTERED)}: C11.1, R25.2, TP4.1, U1.15 (PA4/T14C1/ADC4/USART1_{CK})
/motor_driver/I_{SENSE(RAW)}: Q2.1 (S), Q2.2 (S), Q2.3 (S), Q4.1 (S), Q4.2 (S), Q4.3 (S), Q6.1 (S), Q6.2 (S), Q6.3 (S), R18.1, R27.1
/motor_driver/I_{SENSE(RAW)}_N: R18.3, R24.1, R27.3, TP2.1
/motor_driver/I_{SENSE(RAW)}_P: R18.2, R22.1, R26.1, R27.2, TP1.1
/motor_driver/LED_{ERROR}: R16.1, U1.40 (PB6/USART1_{TX})
/motor_driver/LED_{FW_READY}: R15.1, U1.41 (PB7/USART1_{RX})
/motor_driver/LED_{WARN}: R8.1, U1.45 (PB8/T16C1)
/motor_driver/MOTOR_{U}: C1.2, J2.2, Q1.1 (S), Q1.2 (S), Q1.3 (S), Q2.5 (D), U1.34 (OUTU)
/motor_driver/MOTOR_{V}: C7.2, J2.3, Q3.1 (S), Q3.2 (S), Q3.3 (S), Q4.5 (D), U1.30 (OUTV)
/motor_driver/MOTOR_{W}: C9.2, J2.1, Q5.1 (S), Q5.2 (S), Q5.3 (S), Q6.5 (D), U1.26 (OUTW)
/motor_driver/NRST: C16.1, J6.10 (~RESET), Q7.3 (D), U1.7 (NRST)
/motor_driver/OSC32_N: C18.1, U1.2 (PC15/OSC32_{OUT}), Y1.1
/motor_driver/OSC32_P: C19.1, U1.1 (PC14/OSC32_{IN}), Y1.2
/motor_driver/OSC_N: C20.1, U1.5 (PF1/OSC_{OUT}), Y2.1
/motor_driver/OSC_P: C21.1, U1.4 (PF0/OSC_{IN}), Y2.3
/motor_driver/SWCLK: J6.4 (SWCLK/TCK), R39.2, U1.38 (PA14/SWDCLK/USART1_{TX}/BL_UART_{TX})
/motor_driver/SWDIO: J6.2 (SWDIO/TMS), U1.37 (PA13/SWDIO)
/motor_driver/VEL_ENC_{~DET}: U1.16 (PA5/ADC5); also elsewhere on the board
/motor_driver/V_{sense}_V_{batt}: R17.2, R38.1, U1.19 (PB1/T3C4/T14C1/ADC9)
GND: C2.2, C3.2, C4.2, C5.2, C6.2, C8.2, C10.2, C11.2, C16.2, C18.2, C19.2, C20.2, C21.2, C22.2, C23.2, D3.1 (K), D4.1 (K), D5.1 (K), J4.1, J4.6, J6.3 (GND), J6.5 (GND), J6.9 (GNDDetect), Q7.2 (S), R18.4, R20.2, R27.4, R36.2, R38.2, R43.2, U1.20 (TESTMODE), U1.44 (GND), U1.49 (EPAD), Y2.2 (G), Y2.4 (G); also elsewhere on the board
unnamed: D1.1 (A), R10.1
unnamed: D1.6 (K), R9.1, U1.32 (LSV)
unnamed: D1.2 (A), R1.1
unnamed: D1.5 (K), R2.1, U1.33 (HSU)
unnamed: D1.3 (A), R4.1
unnamed: D1.4 (K), R3.1, U1.36 (LSU)
unnamed: D2.1 (A), R11.1
unnamed: D2.6 (K), R12.1, U1.25 (HSW)
unnamed: D2.2 (A), R14.1
unnamed: D2.5 (K), R13.1, U1.28 (LSW)
unnamed: D2.3 (A), R5.1
unnamed: D2.4 (K), R6.1, U1.29 (HSV)
unnamed: D3.2 (A), R8.2
unnamed: D4.2 (A), R15.2
unnamed: D5.2 (A), R16.2
unnamed: Q1.4 (G), R1.2, R2.2
unnamed: Q2.4 (G), R3.2, R4.2
unnamed: Q3.4 (G), R5.2, R6.2
unnamed: Q4.4 (G), R9.2, R10.2
unnamed: Q5.4 (G), R11.2, R12.2
unnamed: Q6.4 (G), R13.2, R14.2
unnamed: Q7.1 (G), R20.1, R44.2
unnamed: F4.2, U1.8 (VM)
unnamed: C8.1, U1.6 (VREG12)
unnamed: C1.1, U1.35 (VBOOTU)
unnamed: C7.1, U1.31 (VBOOTV)
unnamed: C9.1, U1.27 (VBOOTW)
unnamed: R19.1, R24.2, U1.22 (OP1N)
unnamed: R23.2, R26.2, R36.1, U1.23 (OP1P)
unnamed: C10.1, R21.2, R22.2, R43.1, TP5.1, U1.24 (OC_COMP)

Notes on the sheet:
Halls must be on TIM2 CH1,2,3 Encoders must be on TIM3 CH1,2
GN HALL_{2}
Route inverted side GND close to R_{SENSE}
Indicators
Three-Phase Driver
RD +3.3V
GY MOTOR_{U}
AN C_{LP}
WH HALL_{3}
AN R2
AN R_{a}
BK GND
10A Motor Current, 5A per resistor V_{drop}@5A = 0.500V P_{diss}@5A = 2.5W
AN R1
BK GND/NC
Power Input
AN R_{LP}
BN MOTOR_{V}
YE MOTOR_{W}
AN R_{b}
Current Sense
Motor Logic
External Connections
Debug Header
Clocks
Reset Logic
BU HALL_{1}
See current_sense.asc for LT spice simulation of current sense and OCP network. R_{sense}=50mOhm, current sense set to detect 0 - +10.0A range, up to the peak current rating of nanotec df45 65W with sufficient resolution for 50W as well. Stall current will cause opamp to clip. LPF -3db cutoff rough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
TX and SWCLK are both active drive. SWD/JTAD and upstream AT_UART should not be connected at the same time. Remove R39 to physically isolate SWD.



Board: 6 copper layers, 45.0 x 46.0 mm, 106 parts (57 on the bottom side), 76 nets.

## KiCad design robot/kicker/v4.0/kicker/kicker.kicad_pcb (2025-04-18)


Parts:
J11: JST-BM10B-GHS; JST_GH_BM10B-GHS-TBT_1x10-1MP_P1.25mm_Vertical; LCSC C2683602
R1, R2: 330; R_0402_1005Metric; LCSC C105875
R3, R82, R83, R84: 100k; R_0402_1005Metric; LCSC C60491
TP1: 5v0 US; TestPoint_Pad_D1.0mm
TP2: 3v3 US; TestPoint_Pad_D1.0mm

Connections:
+3V3: R3.1, R82.1; also elsewhere on the board
/3v3_UPSTREAM: J11.2, TP2.1
/5v0_UPSTREAM: J11.1, TP1.1
/COMS.BOOT0: J11.5, R83.1; also elsewhere on the board
/COMS.CTS: J11.10, R82.2; also elsewhere on the board
/COMS.RST: J11.6, R84.1; also elsewhere on the board
/COMS.RTS: R2.2; also elsewhere on the board
/COMS.RX: J11.7, R3.2; also elsewhere on the board
/COMS.TX: R1.2; also elsewhere on the board
/UPSTREAM_GND: J11.3, J11.4
GND: J11.MP (MountPin), R83.2, R84.2; also elsewhere on the board
unnamed: J11.8, R1.1
unnamed: J11.9, R2.1

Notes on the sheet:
Don't make ground loop with the high current xt30
Control Board Connector
"MOSI" pin 5, "MISO" pin 6


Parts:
J7: SM12B-ZESS-TB; JST_ZE_BM12B-ZESS-TBT_1x12-1MP_P1.50mm_Vertical
R69, R71, R80, R81: 100k; R_0402_1005Metric; LCSC C60491
R70, R79: 330; R_0402_1005Metric; LCSC C105875

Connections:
+3V3: J7.12, R69.1, R71.1; also elsewhere on the board
+BATT: J7.1, J7.2; also elsewhere on the board
/Dribbler/DRIB_BOOT_UART.BOOT0: J7.5, R81.1; also elsewhere on the board
/Dribbler/DRIB_BOOT_UART.CTS: J7.9, R69.2; also elsewhere on the board
/Dribbler/DRIB_BOOT_UART.RST: J7.6, R80.1; also elsewhere on the board
/Dribbler/DRIB_BOOT_UART.RTS: R79.1; also elsewhere on the board
/Dribbler/DRIB_BOOT_UART.RX: J7.8, R71.2; also elsewhere on the board
/Dribbler/DRIB_BOOT_UART.TX: R70.1; also elsewhere on the board
GND: J7.3, J7.4, J7.11, R80.2, R81.2; also elsewhere on the board
unnamed: J7.7, R70.2
unnamed: J7.10, R79.2

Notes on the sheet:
Dribbler Motor



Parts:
C6, C7, C10, C12, C13, C14, C15, C16, C18, C24: 100n 50V; C_0402_1005Metric; LCSC C307331
C8, C19: 4.7u 6.3V; C_0402_1005Metric; LCSC C76995
C9: 10n 50V; C_0402_1005Metric; LCSC C77019
C11, C17: 1u 50V; C_0402_1005Metric; LCSC C1518208
C20, C22: 15pF; C_0402_1005Metric; LCSC C88877
C21, C23: 11pF; C_0402_1005Metric; LCSC C161525
D3: PESD3V3L5UY; SOT-363_SC-70-6; LCSC C477992
D4, D6: XL-1608UBC-04; LED0603; LCSC C965807
D5: XL-1608UGC-04; LED0603; LCSC C965804
D7: XL-1608SURC-06; LED0603; LCSC C965799
D8: XL-1608UWC-04; LED0603; LCSC C965808
D9: XL-1608UOC-06; LED0603; LCSC C965800
J4: Conn_ARM_JTAG_SWD_10; Samtec-2x5pin-1.27mm; LCSC C448647
Q1, Q2: BSS138K; SOT-23; LCSC C255592
R11, R16, R17, R18, R19, R25, R26, R27, R30, R31, R32, R35, R43, R44: 10k; R_0402_1005Metric; LCSC C60490
R12, R13, R14, R15, R20: 330; R_0402_1005Metric; LCSC C105875
R21: 100k; R_0402_1005Metric; LCSC C60491
R22: 10k; R_0402_1005Metric; LCSC C60490; not fitted
R23: 0; R_0402_1005Metric; LCSC C106231; not fitted
R24, R28: 0; R_0402_1005Metric; LCSC C106231
R29, R34, R37, R40, R42: 1k; R_0402_1005Metric; LCSC C11702
R33: 11.5k; R_0402_1005Metric; LCSC C270653
R36: 8.06k; R_0402_1005Metric; LCSC C276278
R38: 23.2k; R_0402_1005Metric; LCSC C163477
R39: 1.5k; R_0402_1005Metric; LCSC C25867
R41: 649; R_0402_1005Metric; LCSC C82294
RV1, RV2: 3269P-1-103GLF; Potentiometer_Bourns_3269P_Horizontal
SW1: BTN0; SW_SPST_TL3305A; LCSC C2886902
SW2: SW_DIP_x04; CHP-041TB
SW3: RST; SW_SPST_TL3305A; LCSC C2886902
U3: STM32G474VETx; LQFP-100_14x14mm_P0.5mm; LCSC C431632
U4, U6: SK9822; LCSC C2829089
U5: AT25DF041x-UxN-x; SOIC-8_3.9x4.9mm_P1.27mm; not fitted
Y1: Q13FC13500005; Crystal_SMD_3215-2Pin_3.2x1.5mm; LCSC C841881
Y2: TAXM8M4RDBCCT2T; Crystal_SMD_3225-4Pin_3.2x2.5mm; LCSC C400090

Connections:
+3V0: C9.1, C11.1, C15.1, C17.1, U3.36 (VREF+), U3.37 (VDDA); also elsewhere on the board
+3V3: C8.2, C10.1, C12.1, C13.1, C14.1, C16.1, C24.2, J4.1 (VTref), R22.1, R30.1, R32.1, R41.1, RV1.1, RV2.1, SW1.2, SW2.5, SW2.6, SW2.7, SW2.8, U3.6 (VBAT), U3.24 (VDD), U3.49 (VDD), U3.64 (VDD), U3.75 (VDD), U3.100 (VDD), U5.3 (~WP/IO2), U5.7 (~HOLD/IO3), U5.8 (VCC); also elsewhere on the board
+5V: C19.2, R39.1, U4.4 (VCC), U6.4 (VCC); also elsewhere on the board
+BATT: R33.1, R38.1; also elsewhere on the board
+VSW: R36.1; also elsewhere on the board
/Ball Sense/SENSE_BOOT_UART.BOOT0: U3.89 (PD7); also elsewhere on the board
/Ball Sense/SENSE_BOOT_UART.CTS: U3.85 (PD3); also elsewhere on the board
/Ball Sense/SENSE_BOOT_UART.RST: U3.90 (PB3); also elsewhere on the board
/Ball Sense/SENSE_BOOT_UART.RTS: U3.86 (PD4); also elsewhere on the board
/Ball Sense/SENSE_BOOT_UART.RX: U3.88 (PD6); also elsewhere on the board
/Ball Sense/SENSE_BOOT_UART.TX: U3.87 (PD5); also elsewhere on the board
/Breakbeam/BB_LEFT.AGPIO: U3.15 (PC0); also elsewhere on the board
/Breakbeam/BB_LEFT.INT: U3.81 (PC12); also elsewhere on the board
/Breakbeam/BB_LEFT.RST: U3.79 (PC10); also elsewhere on the board
/Breakbeam/BB_LEFT.SCL: U3.78 (PA15); also elsewhere on the board
/Breakbeam/BB_LEFT.SDA: U3.94 (PB7); also elsewhere on the board
/Breakbeam/BB_LEFT.~DET: U3.80 (PC11); also elsewhere on the board
/Breakbeam/BB_RIGHT.AGPIO: U3.17 (PC2); also elsewhere on the board
/Breakbeam/BB_RIGHT.INT: U3.57 (PD10); also elsewhere on the board
/Breakbeam/BB_RIGHT.RST: U3.59 (PD12); also elsewhere on the board
/Breakbeam/BB_RIGHT.SCL: U3.65 (PC6); also elsewhere on the board
/Breakbeam/BB_RIGHT.SDA: U3.66 (PC7); also elsewhere on the board
/Breakbeam/BB_RIGHT.~DET: U3.58 (PD11); also elsewhere on the board
/COMS.BOOT0: R27.2, U3.95 (PB8); also elsewhere on the board
/COMS.CTS: U3.72 (PA11); also elsewhere on the board
/COMS.RST: Q1.1 (G), R21.1; also elsewhere on the board
/COMS.RTS: U3.73 (PA12); also elsewhere on the board
/COMS.RX: U3.71 (PA10); also elsewhere on the board
/COMS.TX: U3.70 (PA9); also elsewhere on the board
/Dribbler/DRIB_BOOT_UART.BOOT0: U3.44 (PE13); also elsewhere on the board
/Dribbler/DRIB_BOOT_UART.CTS: U3.52 (PB13); also elsewhere on the board
/Dribbler/DRIB_BOOT_UART.RST: U3.45 (PE14); also elsewhere on the board
/Dribbler/DRIB_BOOT_UART.RTS: U3.53 (PB14); also elsewhere on the board
/Dribbler/DRIB_BOOT_UART.RX: U3.46 (PE15); also elsewhere on the board
/Dribbler/DRIB_BOOT_UART.TX: U3.47 (PB10); also elsewhere on the board
/Power Regulation/VSW_PGOOD: U3.42 (PE11); also elsewhere on the board
/digital/BB_LED_DRAIN: D4.1 (K), D6.1 (K), Q2.3 (D)
/digital/CMD_{CHG}: U3.54 (PB15); also elsewhere on the board
/digital/CMD_{CHIP}: U3.55 (PD8); also elsewhere on the board
/digital/CMD_{KICK}: U3.56 (PD9); also elsewhere on the board
/digital/DIP0: R15.2, U3.82 (PD0)
/digital/DIP1: R14.2, U3.83 (PD1)
/digital/DIP2: R13.2, U3.84 (PD2)
/digital/DIP3: R12.2, U3.3 (PE4)
/digital/DOTSTAR_MOSI: U3.5 (PE6), U4.1 (SDI)
/digital/DOTSTAR_SCK: U3.1 (PE2), U4.2 (CKI)
/digital/FLASH_MISO: U3.28 (PA6), U5.2 (SO/IO1)
/digital/FLASH_MOSI: U3.29 (PA7), U5.5 (SI/IO0)
/digital/FLASH_NSS: U3.26 (PA4), U5.1 (~CS)
/digital/FLASH_SCK: U3.27 (PA5), U5.6 (SCK)
/digital/LED_BB_BLUE: Q2.1 (G), R43.2, U3.98 (PE1)
/digital/LED_GREEN: R31.1, U3.96 (PB9)
/digital/LED_RED: R35.1, U3.97 (PE0)
/digital/NRST: C7.1, D3.1 (K1), J4.10 (~RESET), Q1.3 (D), R22.2, SW3.2, U3.14 (PG10)
/digital/OPAMP3_VIN+: R24.2, U3.32 (PB0)
/digital/OPAMP3_VIN-: R25.1, R26.1, U3.34 (PB2)
/digital/OPAMP3_VOUT: R26.2, R28.1, U3.33 (PB1)
/digital/RCC_OSC32_N: C20.1, U3.9 (PC15), Y1.1
/digital/RCC_OSC32_P: C22.1, U3.8 (PC14), Y1.2
/digital/RCC_OSC_N: C21.1, U3.13 (PF1), Y2.1
/digital/RCC_OSC_P: C23.1, U3.12 (PF0), Y2.3
/digital/SWCLK: D3.3 (K2), J4.4 (SWCLK/TCK), U3.77 (PA14)
/digital/SWDIO: D3.4 (K3), J4.2 (SWDIO/TMS), U3.76 (PA13)
/digital/ShutdownInitiated: R44.1, U3.93 (PB6)
/digital/USER_ADJ1: RV1.2, U3.39 (PE8)
/digital/USER_ADJ2: RV2.2, U3.40 (PE9)
/digital/USR_BTN: D3.6 (K5), R20.1, U3.92 (PB5)
/digital/VSW_EN: U3.41 (PE10); also elsewhere on the board
/digital/V_{sense}_3v3: R41.2, R42.1, U3.25 (PA3)
/digital/V_{sense}_5V0: R39.2, R40.1, U3.22 (PA2)
/digital/V_{sense}_HV: D3.5 (K4), R23.1, R24.1; also elsewhere on the board
/digital/V_{sense}_HV_FILT: C18.1, R29.2, U3.18 (PC3)
/digital/V_{sense}_HV_PREFILT: R23.2, R28.2, R29.1
/digital/V_{sense}_VSW: R36.2, R37.1, U3.21 (PA1)
/digital/V_{sense}_V_{batt}: R33.2, R34.1, U3.20 (PA0)
GND: C6.2, C7.2, C8.1, C9.2, C10.2, C11.2, C12.2, C13.2, C14.2, C15.2, C16.2, C17.2, C18.2, C19.1, C20.2, C21.2, C22.2, C23.2, C24.1, D3.2 (A), D5.1 (K), D7.1 (K), D8.1 (K), D9.1 (K), J4.3 (GND), J4.5 (GND), J4.9 (GNDDetect), Q1.2 (S), Q2.2 (S), R11.2, R16.1, R17.1, R18.1, R19.1, R21.2, R25.2, R27.1, R34.2, R37.2, R40.2, R42.2, R43.1, RV1.3, RV2.3, SW3.1, U3.23 (VSS), U3.35 (VSSA), U3.48 (VSS), U3.63 (VSS), U3.74 (VSS), U3.99 (VSS), U4.3 (GND), U5.4 (GND), U6.3 (GND), Y2.2, Y2.4; also elsewhere on the board
unnamed: C6.1, R11.1, R20.2, SW1.1
unnamed: D4.2 (A), R30.2
unnamed: D5.2 (A), R31.2
unnamed: D6.2 (A), R32.2
unnamed: D7.2 (A), R35.2
unnamed: D8.2 (A), R38.2
unnamed: D9.2 (A), R44.2
unnamed: R12.1, R16.2, SW2.4
unnamed: R13.1, R17.2, SW2.3
unnamed: R14.1, R18.2, SW2.2
unnamed: R15.1, R19.2, SW2.1
unnamed: U4.5 (CKO), U6.2 (CKI)
unnamed: U4.6 (SDO), U6.1 (SDI)

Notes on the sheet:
Peripherial Maps: BOOT: USART1 BALL SENSE: USART2 DRIBBLER: USART3 FLASH: SPI1 DOTSTAR: SPI4 BRK BEAM L: I2C1 BRK BEAM C: I2C3 BRK BEAM R: I2C4 Pin Alternate/Multi Functions: High Voltage Kick: PE5 - Digital Out - HRTIM_CHD1 PWM Gen. High Voltage Chip: PE6 - Digital Out - HRTIM_CHC2 Gen. Brk Beam L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
There are four modes of operation to sense V_{solenoid} 1. No Amplification - Populate R28, de-populate R27,R30 - Disable the amplifier in firmware 2. External Mode (OPAMP3) - Populate R27,R30, de-populate R28 - Set OPAMP3 to external mode in firmware - Read V_{sense}_HV on PC3 (ADC1 IN9) 3. Progra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
User DIP SW
Microcontroller
User Trim Pots
Clocks
-3dB cutoff 1.6kHz
Flash Chip
Debug Header
DOTSTAR_MISO
User Button
Charge Level
stm32 has calibrated internal pull-up to sequence
OPAMP3
G=2
uC Decoupling
Voltage Monitoring
V_{sense}_HV_FB
H to L Nets
I_{out}@200V= 68uA I_{out}@20V = 6.8uA I_{out}@2V = 0.68uA
V_{solenoid} Voltage Measurement
Status
TVS Protection
Reset Logic
V_{sense}_HV_AMPED
Software Indicators
DOTSTAR_NSS


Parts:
H1, H2, H3: M3; MountingHole_3.2mm_M3_Pad



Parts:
C1: 0.1u; C_0402_1005Metric; LCSC C307331
C2: 1u; C_1206_3216Metric; LCSC C1848
C3: 1u 50V; C_0402_1005Metric; LCSC C1518208
C4: 10n 50V; C_0402_1005Metric; LCSC C77019
C5: 10u 50V; C_0805_2012Metric; LCSC C440198
D1: 824521261; D_SMB_Non-Polar; LCSC C3708253
D2: 1N4001; D_SMA; LCSC C2909965
F1, F2: Fuse_0603_1608Metric_Pad1.05x0.95mm_HandSolder; LCSC C187605
F3: 10A; 3557-2; LCSC C352820
F4: 06F-0200L1; Fuse_0603_1608Metric_Pad1.05x0.95mm_HandSolder; LCSC C377220
F5: 0467.250NRHF; Fuse_0603_1608Metric_Pad1.05x0.95mm_HandSolder; LCSC C151137
J2: BM04B-PASS-1-TFT; JST_PA_BM04B-PASS_1x04_P2.00_Vertical; LCSC C265298
J3: XT30-M; AMASS_XT30U-M_1x02_P5.0mm_Vertical; LCSC C99102
JP1: 3v0 Local Enable; SolderJumper-2_2.0x1.2mm_Closed
JP2: 18v0 Local Enable; SolderJumper-2_2.0x1.2mm_Closed
L1: 650 @100MHz; R_0603_1608Metric; LCSC C21189
R4: 1.47M; R_0805_2012Metric; LCSC C189666
R5: 0; R_0402_1005Metric; LCSC C106231; not fitted
R6: 0; R_0402_1005Metric; LCSC C106231
R7, R10: 10k; R_0402_1005Metric; LCSC C60490
R8: 26.1k; R_0402_1005Metric; LCSC C102932
R9: 1k; R_0402_1005Metric; LCSC C11702
U1: TLV70030_SOT353; SOT-353_SC-70-5; LCSC C527437
U2: TPS7B86; Texas_HSOP-8-1EP_3.9x4.9mm_P1.27mm; LCSC C5189739

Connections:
+3V0: F4.2; also elsewhere on the board
+3V3: F2.2, L1.1, R10.1; also elsewhere on the board
+5V: F1.2; also elsewhere on the board
+BATT: C3.2, D1.2 (A2), D2.1 (K), F3.2, R4.2, R5.1, U2.8 (IN); also elsewhere on the board
+VSW: F5.2; also elsewhere on the board
/Power Regulation/3v0_PREFUSE: C2.1, JP1.1 (A), U1.5 (OUT)
/Power Regulation/3v3_FILT: C1.1, L1.2, U1.1 (IN), U1.3 (EN)
/Power Regulation/VSW_CEN: R5.2, R6.2, R7.1, U2.7 (EN)
/Power Regulation/VSW_FB: R8.2, R9.1, U2.2 (FB)
/Power Regulation/VSW_PGOOD: R10.2, U2.6 (PG); also elsewhere on the board
/Power Regulation/V_{batt}: F3.1, J3.2
/digital/VSW_EN: R6.1; also elsewhere on the board
GND: C1.2, C2.2, C3.1, C4.2, C5.1, D1.1 (A1), J2.3, J2.4, J3.1, R4.1, R7.2, R9.2, U1.2 (GND), U2.5 (GND), U2.9 (GND); also elsewhere on the board
unnamed: C5.2, D2.2 (A), JP2.1 (A), R8.1, U2.1 (OUT)
unnamed: F1.1, J2.1
unnamed: F2.1, J2.2
unnamed: F4.1, JP1.2 (B)
unnamed: F5.1, JP2.2 (B)
unnamed: C4.1, U2.3 (DELAY)

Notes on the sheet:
Drop out voltage TPS7B8601 Thermal Calcs: - ambient temp of 40C (104F) - junction to ambient thermal rise of 60.2 C/W - full battery 25.2 V - output voltage 18.0V - sustained fused current (I) draw of 250 mA - T = Tamb + Tja * (25.2 - 18.0) * I - T = 40 + 41.8 * (25.2 - 18.0) * 0.250 - T = 115.24 C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
Power Budget 18.0V: 250 mA available ~95mA LT3757 Vccint max continuous draw during regulation ~100mA IGBT drive "continuous" draw ~200mA TOTAL 3.3V: 3.0A available 200mA stm32f411 100mA LEDs + Switches 200mA Dribbler Motor 200mA Sense Board 50mA Breakbeam 750mA TOTAL 5.0V 1.0A Available ~100mA Dot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
0.65V ref
8ms delay
3.0V Local Power
Low Voltage Power
200mA

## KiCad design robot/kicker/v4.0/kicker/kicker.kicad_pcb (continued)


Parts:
J8, J9: SM08B-GHS-TB; JST_GH_SM08B-GHS-TB_1x08-1MP_P1.25mm_Horizontal
R72, R73, R74, R75: 2.1k; R_0402_1005Metric; LCSC C25877

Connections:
+3V3: J8.1, J9.1, R72.1, R73.1, R74.1, R75.1; also elsewhere on the board
/Breakbeam/BB_LEFT.AGPIO: J9.2; also elsewhere on the board
/Breakbeam/BB_LEFT.INT: J9.8; also elsewhere on the board
/Breakbeam/BB_LEFT.RST: J9.6; also elsewhere on the board
/Breakbeam/BB_LEFT.SCL: J9.5, R75.2; also elsewhere on the board
/Breakbeam/BB_LEFT.SDA: J9.4, R73.2; also elsewhere on the board
/Breakbeam/BB_LEFT.~DET: J9.7; also elsewhere on the board
/Breakbeam/BB_RIGHT.AGPIO: J8.2; also elsewhere on the board
/Breakbeam/BB_RIGHT.INT: J8.8; also elsewhere on the board
/Breakbeam/BB_RIGHT.RST: J8.6; also elsewhere on the board
/Breakbeam/BB_RIGHT.SCL: J8.5, R74.2; also elsewhere on the board
/Breakbeam/BB_RIGHT.SDA: J8.4, R72.2; also elsewhere on the board
/Breakbeam/BB_RIGHT.~DET: J8.7; also elsewhere on the board
GND: J8.3, J9.3; also elsewhere on the board

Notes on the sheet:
Breakbeam Breakouts


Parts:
J1: JST-SM10B-GHS; JST_GH_SM10B-GHS-TB_1x10-1MP_P1.25mm_Horizontal; LCSC C2683602
R76, R77, R86, R87: 100k; R_0402_1005Metric; LCSC C60491
R78, R85: 330; R_0402_1005Metric; LCSC C105875

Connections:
+3V3: J1.2, R76.1, R77.1; also elsewhere on the board
+5V: J1.1; also elsewhere on the board
/Ball Sense/SENSE_BOOT_UART.BOOT0: J1.5, R87.1; also elsewhere on the board
/Ball Sense/SENSE_BOOT_UART.CTS: J1.9, R76.2; also elsewhere on the board
/Ball Sense/SENSE_BOOT_UART.RST: J1.6, R86.1; also elsewhere on the board
/Ball Sense/SENSE_BOOT_UART.RTS: R85.1; also elsewhere on the board
/Ball Sense/SENSE_BOOT_UART.RX: J1.8, R77.2; also elsewhere on the board
/Ball Sense/SENSE_BOOT_UART.TX: R78.1; also elsewhere on the board
GND: J1.3, J1.4, J1.MP (MountPin), R86.2, R87.2; also elsewhere on the board
unnamed: J1.7, R78.2
unnamed: J1.10, R85.2

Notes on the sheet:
Ball Sense Connector


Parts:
C25, C26: ESMQ201VSN152MR35S; CP_Radial_D30.0mm_P10.00mm_SnapIn
D10, D11: XL-1608SURC-06; LED0603; LCSC C965799
R45, R46, R47, R48, R49, R50: 1.47M; R_0805_2012Metric; LCSC C189666
R51: 14.7k; R_0402_1005Metric; LCSC C25856

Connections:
/digital/V_{sense}_HV: R50.2, R51.1; also elsewhere on the board
/hv_kicker/DL1S: R45.2, R46.1
/hv_kicker/DL2S: R47.2, R48.1
/hv_kicker/HVMS: R49.2, R50.1
/hv_kicker/flyback_charger/V_{solenoid}: C25.1, C26.1, R45.1, R47.1, R49.1; also elsewhere on the board
GND: C25.2, C26.2, D10.1 (K), D11.1 (K), R51.2; also elsewhere on the board
unnamed: D10.2 (A), R46.2
unnamed: D11.2 (A), R48.2

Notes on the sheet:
0.995V ref at 200V rail 1.990V ref at 200V rail, G_{amp}=2.0 1.890V ref at 190V rail, G_{amp}=2.0 1.792V ref at 180V rail, G_{amp}=2.0
Solenoid Impulse Circuit
DEATHLIGHT
Energy Bank
If using alternatives, height must be less than or equal to 50mm

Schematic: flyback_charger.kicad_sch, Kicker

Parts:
C29: REH1020471M050K; CP_Radial_H_InPlane_D10.00mm_H22.00mm_P5.00mm
C30, C32, C33, C36, C38: 10u 50V; C_0805_2012Metric; LCSC C440198
C31: 10n 50V; C_0402_1005Metric; LCSC C77019
C34, C35: 100n 50V; C_0402_1005Metric; LCSC C307331
C37: 6.8n 50V; C_0402_1005Metric; LCSC C93654
C39: 4.7u 50V; C_0805_2012Metric; LCSC C162420
C40: 100n 200V; C_0805_2012Metric; LCSC C784084
C41: 100n 500V; C_1210_3225Metric; LCSC C440207
D14: HS5M; D_SMC; LCSC C2944264
L2: GA3460-BL; GA34XX-BL
Q5: BSC0402NSATMA1; TDSON-8-1
R58: 1k; R_0402_1005Metric; LCSC C11702
R59: 140k; R_0402_1005Metric; LCSC C270645
R60: 22k; R_0402_1005Metric; LCSC C25768
R61: 1; R_0805_2012Metric; LCSC C2907233
R62: 100k; R_0402_1005Metric; LCSC C60491
R63: 10; R_0402_1005Metric; LCSC C138066
R64, R65: PE1206FRM470R008L; R_1206_3216Metric; LCSC C473031
R66, R67: 976k 0.1%; R_0805_2012Metric; LCSC C229056
R68: 17.4k 0.1%; R_0402_1005Metric; LCSC C517755
R88: 0; R_0402_1005Metric; LCSC C106231; not fitted
TP3: CHG_EN; TestPoint_Pad_D1.5mm
TP4: SPICE: V_{drain} <<<HIGH VOLTAGE>>>; TestPoint_Pad_D1.5mm
TP5: FB; TestPoint_Pad_D1.5mm
TP6: SPICE: V_{out} <<<HIGH VOLTAGE>>>; TestPoint_Pad_D1.5mm
U8: LT3757EMSE; MSOP-10-1EP_3x3mm_P0.5mm_EP1.68x1.88mm; LCSC C580135

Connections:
+BATT: C29.1, C30.1, C32.1, C33.1, C35.1, C36.1, C38.1, L2.9, L2.10, L2.11, L2.12, R61.1, U8.10 (VIN); also elsewhere on the board
+VSW: R88.2; also elsewhere on the board
/digital/CMD_{CHG}: R58.1, TP3.1, U8.9 (~SHDN/UVLO); also elsewhere on the board
/hv_kicker/flyback_charger/CSP: Q5.1 (S), Q5.2 (S), Q5.3 (S), R64.2, R65.2, U8.6 (SENSE)
/hv_kicker/flyback_charger/FB: R67.1, R68.2, TP5.1, U8.2 (FBX)
/hv_kicker/flyback_charger/HVFBS: R66.1, R67.2
/hv_kicker/flyback_charger/HVGATE: R62.2, R63.1, U8.7 (GATE)
/hv_kicker/flyback_charger/HV_AC: D14.2 (A), L2.7
/hv_kicker/flyback_charger/V_{solenoid}: C41.1, D14.1 (K), R66.2, TP6.1; also elsewhere on the board
/hv_kicker/flyback_charger/V_{trans}: C40.2, L2.1, L2.2, L2.3, L2.4, Q5.5 (D), TP4.1
GND: C29.2, C30.2, C31.2, C32.2, C33.2, C34.2, C35.2, C36.2, C37.2, C38.2, C39.2, C41.2, L2.6, R58.2, R59.1, R62.1, R64.1, R65.1, R68.1, U8.5 (SYNC), U8.11 (GND); also elsewhere on the board
unnamed: C37.1, R60.1
unnamed: C40.1, R61.2
unnamed: Q5.4 (G), R63.2
unnamed: C39.1, R88.1, U8.8 (INTVCC)
unnamed: R59.2, U8.4 (RT)
unnamed: C31.1, U8.3 (SS)
unnamed: C34.1, R60.2, U8.1 (VC)

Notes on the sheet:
DO NOT blindly copy and modify this schematic according to the datasheet. Spice simulation of this circuit with GA3459 and GA3460 inductors, with leakeage modeled, has shown very high sensitivty to snubber values. Failure to model changes to any core component of the flyback system (transformer, sw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
Switching Freq. 100kHz
High Voltage Regulator
LAYOUT NOTE: LT3751 instructs designs to place fast response decoupling very close the transformer primary to minimize leakage inductance.
Control IO Config
6S LiPo (19.2V-25.2V)
~190.0V-195.0V
12.0V-24.0V
External IO Specs
!!IMPORTANT!!: You must strictly power sequence INTV_{cc} AFTER V_{in}.
V_{logic} nominal, V_{cc} max 100k pull down
Transformer Primary Side Decoupling
RC Snubber

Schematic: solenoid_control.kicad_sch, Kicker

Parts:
C27: 10u 50V; C_0805_2012Metric; LCSC C440198
C28: 100n 50V; C_0402_1005Metric; LCSC C307331
D12, D13: MURS460; D_SMC; LCSC C961891
J5, J6: 2165711002
Q3, Q4: IXGA48N60A3; TO-263-2
R52, R53: 10k; R_0402_1005Metric; LCSC C60490
R54, R55: 100k; R_0402_1005Metric; LCSC C60491
R56, R57: 10; R_0402_1005Metric; LCSC C138066
U7: IX4427; SOIC-8_3.9x4.9mm_P1.27mm; LCSC C171845

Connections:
+VSW: C27.1, C28.1, U7.6 (V+); also elsewhere on the board
/digital/CMD_{CHIP}: R53.1, U7.4 (INB); also elsewhere on the board
/digital/CMD_{KICK}: R52.1, U7.2 (INA); also elsewhere on the board
/hv_kicker/flyback_charger/V_{solenoid}: D12.1 (K), D13.1 (K), J5.1, J6.2; also elsewhere on the board
/hv_kicker/solenoid_control/CHIP_SW: D13.2 (A), J6.1, Q4.2 (C)
/hv_kicker/solenoid_control/GATE_{chip}: R55.1, R57.1, U7.5 (OUTB)
/hv_kicker/solenoid_control/GATE_{chip}_FILT: Q4.1 (G), R57.2
/hv_kicker/solenoid_control/GATE_{kick}: R54.1, R56.1, U7.7 (OUTA)
/hv_kicker/solenoid_control/GATE_{kick}_FILT: Q3.1 (G), R56.2
/hv_kicker/solenoid_control/KICK_SW: D12.2 (A), J5.2, Q3.2 (C)
GND: C27.2, C28.2, Q3.3 (E), Q4.3 (E), R52.2, R53.2, R54.2, R55.2, U7.3 (GND); also elsewhere on the board

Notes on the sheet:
Solenoid DC Resistance Must be >= 1.7 Ohms
IGBT Driver
12.0V-20.0V
V_{logic}, 100k pull down
External IO Specs
Discharge Circuit
Package_TO_SOT_THT:TO-247-3_Horizontal_TabDown: IXXH110N65C4 D2PAK: IXGA48N60A3-TRL 120A 600V
<=250.0V
V_{logic} = 3.3V nominal (1.8V-V_{cc})



Board: 6 copper layers, 172.6 x 120.0 mm, 191 parts (56 on the bottom side), 134 nets.

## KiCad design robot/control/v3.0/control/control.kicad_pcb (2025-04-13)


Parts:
F2: 4A; Fuse_1206_3216Metric_Pad1.42x1.75mm_HandSolder
J6: SM12B-ZESS; JST_ZE_SM12B-ZESS-TB_1x12-1MP_P1.50mm_Horizontal
R26, R27, R30, R31: 100k; R_0402_1005Metric
R28, R29: 330; R_0402_1005Metric

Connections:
+3V3: J6.12, R26.1, R27.1; also elsewhere on the board
+BATT: F2.1; also elsewhere on the board
/back_right_drive_motor/MOTOR.BOOT0: J6.5, R31.1; also elsewhere on the board
/back_right_drive_motor/MOTOR.CTS: J6.9, R26.2; also elsewhere on the board
/back_right_drive_motor/MOTOR.RST: J6.6, R30.1; also elsewhere on the board
/back_right_drive_motor/MOTOR.RTS: R29.1; also elsewhere on the board
/back_right_drive_motor/MOTOR.RX: J6.8, R27.2; also elsewhere on the board
/back_right_drive_motor/MOTOR.TX: R28.1; also elsewhere on the board
GND: J6.3, J6.4, J6.11, R30.2, R31.2; also elsewhere on the board
unnamed: F2.2, J6.1, J6.2
unnamed: J6.7, R28.2
unnamed: J6.10, R29.2

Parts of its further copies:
F1, F3, F4: 4A; Fuse_1206_3216Metric_Pad1.42x1.75mm_HandSolder
J3, J7, J8: SM12B-ZESS; JST_ZE_SM12B-ZESS-TB_1x12-1MP_P1.50mm_Horizontal
R16, R17, R20, R21, R32, R33, R36, R37, R38, R39, R42, R43: 100k; R_0402_1005Metric
R18, R19, R34, R35, R40, R41: 330; R_0402_1005Metric

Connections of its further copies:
+3V3: J3.12, J7.12, J8.12, R16.1, R17.1, R32.1, R33.1, R38.1, R39.1; also elsewhere on the board
+BATT: F1.1, F3.1, F4.1; also elsewhere on the board
/back_left_drive_motor/MOTOR.BOOT0: J7.5, R37.1; also elsewhere on the board
/back_left_drive_motor/MOTOR.CTS: J7.9, R32.2; also elsewhere on the board
/back_left_drive_motor/MOTOR.RST: J7.6, R36.1; also elsewhere on the board
/back_left_drive_motor/MOTOR.RTS: R35.1; also elsewhere on the board
/back_left_drive_motor/MOTOR.RX: J7.8, R33.2; also elsewhere on the board
/back_left_drive_motor/MOTOR.TX: R34.1; also elsewhere on the board
/front_left_drive_motor/MOTOR.BOOT0: J8.5, R43.1; also elsewhere on the board
/front_left_drive_motor/MOTOR.CTS: J8.9, R38.2; also elsewhere on the board
/front_left_drive_motor/MOTOR.RST: J8.6, R42.1; also elsewhere on the board
/front_left_drive_motor/MOTOR.RTS: R41.1; also elsewhere on the board
/front_left_drive_motor/MOTOR.RX: J8.8, R39.2; also elsewhere on the board
/front_left_drive_motor/MOTOR.TX: R40.1; also elsewhere on the board
/front_right_drive_motor/MOTOR.BOOT0: J3.5, R21.1; also elsewhere on the board
/front_right_drive_motor/MOTOR.CTS: J3.9, R16.2; also elsewhere on the board
/front_right_drive_motor/MOTOR.RST: J3.6, R20.1; also elsewhere on the board
/front_right_drive_motor/MOTOR.RTS: R19.1; also elsewhere on the board
/front_right_drive_motor/MOTOR.RX: J3.8, R17.2; also elsewhere on the board
/front_right_drive_motor/MOTOR.TX: R18.1; also elsewhere on the board
GND: J3.3, J3.4, J3.11, J7.3, J7.4, J7.11, J8.3, J8.4, J8.11, R20.2, R21.2, R36.2, R37.2, R42.2, R43.2; also elsewhere on the board
unnamed: F1.2, J3.1, J3.2
unnamed: J3.7, R18.2
unnamed: J3.10, R19.2
unnamed: F3.2, J7.1, J7.2
unnamed: J7.7, R34.2
unnamed: J7.10, R35.2
unnamed: F4.2, J8.1, J8.2
unnamed: J8.7, R40.2
unnamed: J8.10, R41.2

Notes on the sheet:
Default State: BOOT0: pull-down, downstream does not enter the bootloader by default RST: pull-down, the downstream is not in reset by default TX: current limit in the event the downstream device is in push-pull RX: pull-up, the downstream signals idle dataflow if disconencted CTS: pull-up, the dow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
Motor Connector


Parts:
C30: 0.1u; C_0402_1005Metric
C31: 1u; C_1206_3216Metric
D1: SMBJ26CA; D_SMB_Non-Polar
D2: XL-1608UWC-04; LED0603
F6, F7: Fuse_0603_1608Metric_Pad1.05x0.95mm_HandSolder
F8: 06F-0200L1; Fuse_0603_1608Metric_Pad1.05x0.95mm_HandSolder
J11: EC3-M; AMASS_XT30U-M_1x02_P5.0mm_Vertical
J12: JST-GH-SM05B; JST_GH_SM05B-GHS-TB_1x05-1MP_P1.25mm_Horizontal
J13: Conn_01x04; JST_PA_SM04B-PASS_1x04_P2.00mm_Horizontal
JP1: 3v0 Local Enable; SolderJumper-2_2.0x1.2mm_Closed
L1: 650 @100MHz; R_0603_1608Metric
R56: 100k; R_0402_1005Metric
R57: 23.7k; R_0402_1005Metric
R58: 330; R_0402_1005Metric
U3: TLV70030_SOT353; SOT-353_SC-70-5

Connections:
+3V0: F8.2; also elsewhere on the board
+3V3: F7.2, L1.1, R56.1; also elsewhere on the board
+5V: F6.2; also elsewhere on the board
+BATT: D1.2 (A2), J11.2, R57.1; also elsewhere on the board
/mcu/POWER.RX: J12.1, R56.2; also elsewhere on the board
/mcu/POWER.TX: R58.2; also elsewhere on the board
/power/3v0_PREFUSE: C31.1, JP1.1 (A), U3.5 (OUT)
/power/3v3_FILT: C30.1, L1.2, U3.1 (IN), U3.3 (EN)
GND: C30.2, C31.2, D1.1 (A1), D2.1 (K), J11.1, J12.5, J13.3, J13.4, U3.2 (GND); also elsewhere on the board
unnamed: D2.2 (A), R57.2
unnamed: J12.2, R58.1
unnamed: F6.1, J13.1
unnamed: F7.1, J13.2
unnamed: F8.1, JP1.2 (B)

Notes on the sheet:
200mA
Power Board Data Connection
1: PWR TX/MOSI, CTRL RX 2: PWR RX/MISO, CTRL TX 3: PWR SCK, CTRL SCK 4: PWR NSS, CTRL NSS 5: PWR/CTRL GND
Low Voltage Power
Power Input
3.0V Local Power


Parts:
J10: Conn_01x10_MountingPin; JST_GH_SM10B-GHS-TB_1x10-1MP_P1.25mm_Horizontal
R50, R51, R54, R55: 100k; R_0402_1005Metric
R52, R53: 330; R_0402_1005Metric

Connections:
+3V3: J10.2, R50.1, R51.1; also elsewhere on the board
+5V: J10.1; also elsewhere on the board
/mcu/OPTICAL_FLOW.BOOT0: J10.5, R55.1; also elsewhere on the board
/mcu/OPTICAL_FLOW.CTS: J10.9, R50.2; also elsewhere on the board
/mcu/OPTICAL_FLOW.RST: J10.6, R54.1; also elsewhere on the board
/mcu/OPTICAL_FLOW.RTS: R53.1; also elsewhere on the board
/mcu/OPTICAL_FLOW.RX: J10.8, R51.2; also elsewhere on the board
/mcu/OPTICAL_FLOW.TX: R52.1; also elsewhere on the board
GND: J10.3, J10.4, J10.MP (MountPin), R54.2, R55.2; also elsewhere on the board
unnamed: J10.7, R52.2
unnamed: J10.10, R53.2

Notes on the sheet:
Optical Flow Connector


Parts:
C28, C29: 0.1uF 63V; C_0402_1005Metric
J4: BM11B-SRSS-TB; JST_SH_BM11B-SRSS-TB_1x11-1MP_P1.00mm_Vertical
R22, R23: 330; R_0402_1005Metric
R24, R25: 10k; R_0402_1005Metric
U2: BMI323

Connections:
+3V3: C28.1, C29.1, J4.11, R24.1, R25.1, U2.5 (VDDIO), U2.8 (VDD); also elsewhere on the board
/imu/IMU.INT1: J4.4, R22.2, R24.2; also elsewhere on the board
/imu/IMU.INT2: J4.3, R23.2, R25.2; also elsewhere on the board
/imu/IMU.MISO: J4.6, U2.1 (SDO); also elsewhere on the board
/imu/IMU.MOSI: J4.7, U2.14 (SDx); also elsewhere on the board
/imu/IMU.SCK: J4.5, U2.13 (SCx); also elsewhere on the board
/imu/IMU.~DET: J4.2; also elsewhere on the board
/imu/IMU.~SS0: U2.12 (CSB); also elsewhere on the board
/imu/IMU.~SS1: J4.10; also elsewhere on the board
/imu/IMU.~SS2: J4.9; also elsewhere on the board
/imu/IMU.~SS3: J4.8; also elsewhere on the board
GND: C28.2, C29.2, J4.1, J4.MP (MountPin), U2.6 (GNDIO), U2.7 (GND); also elsewhere on the board
unnamed: R22.1, U2.4 (INT1)
unnamed: R23.1, U2.9 (INT2)

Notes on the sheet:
On-Board IMU
IMU Module Communication


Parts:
J15: Conn_02x05_Odd_Even; PinHeader_2x05_P2.54mm_Vertical
Q4: BSS138K; SOT-23
R119: 100k; R_0402_1005Metric

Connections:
+5V: J15.9; also elsewhere on the board
/display/LCD.RST: Q4.1 (G), R119.1; also elsewhere on the board
/display/LCD.RX: J15.7; also elsewhere on the board
/display/LCD.TX: J15.5; also elsewhere on the board
GND: J15.3, J15.4, Q4.2 (S), R119.2; also elsewhere on the board
unnamed: J15.1, Q4.3 (D)

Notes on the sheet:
Pin 3 is Display TX Pin 5 is Display RX Pin 9 is Display nRST, internally pulled up by 4.7k to TTL=3v3. Active low pulse >2us will reset
Display Connector


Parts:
H1, H2, H3, H4: M3; MountingHole_3.2mm_M3_Pad_TopBottom
H5, H6, H7, H8: M2; MountingHole_2.2mm_M2_DIN965_Pad

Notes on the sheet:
LCD
Radio Mounts
Control Mounting Holes

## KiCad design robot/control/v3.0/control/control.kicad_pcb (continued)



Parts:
C1, C5, C7, C10, C13, C16, C17, C18, C19, C20, C21, C22, C23, C24, C25, C26, C27: 100n 50V; C_0402_1005Metric
C2, C6, C8, C9: 1u 50V; C_0402_1005Metric
C3, C4: 15pF; C_0402_1005Metric
C11, C12: 11pF; C_0402_1005Metric
C14, C15: 2.2uF 10V; C_0603_1608Metric
J1: MEM2067-02-180-00-A
J2: Conn_ARM_JTAG_SWD_10; Samtec-2x5pin-1.27mm
P1: USB_C_Plug_USB2.0; USB_C_Receptacle_Molex_105450-0101
Q1: BSS84; SOT-23
Q2: BSS138K; SOT-23
R1: 330; R_0402_1005Metric
R2: 10k; R_0402_1005Metric; not fitted
R3: 10k; R_0402_1005Metric
R4, R7, R8: 100k; R_0402_1005Metric
R5, R6, R12, R13, R14: 1k; R_0402_1005Metric
R9: 11.5k; R_0402_1005Metric
R10: 1.5k; R_0402_1005Metric
R11: 650; R_0402_1005Metric
R15, R126: 5.1k; R_0402_1005Metric
SW1: A6SN-1104; SW_DIP_SPSTx01_Slide_Omron_A6S-110x_W8.9mm_P2.54mm
SW2: RST; SW_SPST_TL3305A
SW3: SW_DIP_x02; 219-2MST
U1: STM32H723ZGTx; LQFP-144_20x20mm_P0.5mm
Y1: Q13FC13500005; Crystal_SMD_3215-2Pin_3.2x1.5mm
Y2: TAXM8M4RDBCCT2T; Crystal_SMD_3225-4Pin_3.2x2.5mm

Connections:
+3V0: C7.1, C8.1, C9.1, C10.1, U1.32 (VREF+), U1.33 (VDDA); also elsewhere on the board
+3V3: C1.1, C2.1, C5.1, C6.1, C16.1, C17.1, C18.1, C19.1, C20.1, C21.1, C22.1, C23.1, C24.1, C25.1, C26.1, C27.1, J1.4 (VDD), J2.1 (VTref), R2.1, R4.1, R5.1, R11.1, SW1.1, SW3.1, U1.6 (VBAT), U1.17 (VDD), U1.30 (VDD), U1.39 (VDD), U1.52 (VDD), U1.62 (VDD), U1.72 (VDD), U1.84 (VDD), U1.95 (VDD33USB), U1.108 (VDD), U1.121 (VDD), U1.131 (VDD), U1.143 (PDR_ON), U1.144 (VDD); also elsewhere on the board
+5V: R10.1; also elsewhere on the board
+BATT: R9.1; also elsewhere on the board
/back_left_drive_motor/MOTOR.BOOT0: U1.4 (PE5); also elsewhere on the board
/back_left_drive_motor/MOTOR.CTS: U1.128 (PG13); also elsewhere on the board
/back_left_drive_motor/MOTOR.RST: U1.3 (PE4); also elsewhere on the board
/back_left_drive_motor/MOTOR.RTS: U1.129 (PG14); also elsewhere on the board
/back_left_drive_motor/MOTOR.RX: U1.1 (PE2); also elsewhere on the board
/back_left_drive_motor/MOTOR.TX: U1.2 (PE3); also elsewhere on the board
/back_right_drive_motor/MOTOR.BOOT0: U1.92 (PG7); also elsewhere on the board
/back_right_drive_motor/MOTOR.CTS: U1.132 (PG15); also elsewhere on the board
/back_right_drive_motor/MOTOR.RST: U1.93 (PG8); also elsewhere on the board
/back_right_drive_motor/MOTOR.RTS: U1.127 (PG12); also elsewhere on the board
/back_right_drive_motor/MOTOR.RX: U1.97 (PC7); also elsewhere on the board
/back_right_drive_motor/MOTOR.TX: U1.96 (PC6); also elsewhere on the board
/display/LCD.RST: U1.100 (PA8); also elsewhere on the board
/display/LCD.RX: U1.102 (PA10); also elsewhere on the board
/display/LCD.TX: U1.101 (PA9); also elsewhere on the board
/front_left_drive_motor/MOTOR.BOOT0: U1.15 (PF5); also elsewhere on the board
/front_left_drive_motor/MOTOR.CTS: U1.21 (PF9); also elsewhere on the board
/front_left_drive_motor/MOTOR.RST: U1.14 (PF4); also elsewhere on the board
/front_left_drive_motor/MOTOR.RTS: U1.20 (PF8); also elsewhere on the board
/front_left_drive_motor/MOTOR.RX: U1.18 (PF6); also elsewhere on the board
/front_left_drive_motor/MOTOR.TX: U1.19 (PF7); also elsewhere on the board
/front_right_drive_motor/MOTOR.BOOT0: U1.73 (PB12); also elsewhere on the board
/front_right_drive_motor/MOTOR.CTS: U1.80 (PD11); also elsewhere on the board
/front_right_drive_motor/MOTOR.RST: U1.74 (PB13); also elsewhere on the board
/front_right_drive_motor/MOTOR.RTS: U1.81 (PD12); also elsewhere on the board
/front_right_drive_motor/MOTOR.RX: U1.78 (PD9); also elsewhere on the board
/front_right_drive_motor/MOTOR.TX: U1.77 (PD8); also elsewhere on the board
/imu/IMU.INT1: U1.46 (PB0); also elsewhere on the board
/imu/IMU.INT2: U1.47 (PB1); also elsewhere on the board
/imu/IMU.MISO: U1.42 (PA6); also elsewhere on the board
/imu/IMU.MOSI: U1.43 (PA7); also elsewhere on the board
/imu/IMU.SCK: U1.41 (PA5); also elsewhere on the board
/imu/IMU.~DET: U1.48 (PB2); also elsewhere on the board
/imu/IMU.~SS0: U1.40 (PA4); also elsewhere on the board
/imu/IMU.~SS1: U1.37 (PA3); also elsewhere on the board
/imu/IMU.~SS2: U1.44 (PC4); also elsewhere on the board
/imu/IMU.~SS3: U1.45 (PC5); also elsewhere on the board
/kicker/KICKER.BOOT0: U1.87 (PG2); also elsewhere on the board
/kicker/KICKER.CTS: U1.85 (PD14); also elsewhere on the board
/kicker/KICKER.RST: U1.88 (PG3); also elsewhere on the board
/kicker/KICKER.RTS: U1.86 (PD15); also elsewhere on the board
/kicker/KICKER.RX: U1.141 (PE0); also elsewhere on the board
/kicker/KICKER.TX: U1.142 (PE1); also elsewhere on the board
/mcu/BOOT0: Q1.3 (D), R6.2, R7.1, U1.138 (BOOT0)
/mcu/BOT_ID_DISPLAY.BL: U1.28 (PC2_C); also elsewhere on the board
/mcu/BOT_ID_DISPLAY.BR: U1.29 (PC3_C); also elsewhere on the board
/mcu/BOT_ID_DISPLAY.FL: U1.26 (PC0); also elsewhere on the board
/mcu/BOT_ID_DISPLAY.FR: U1.27 (PC1); also elsewhere on the board
/mcu/BOT_ID_DISPLAY.SrcDisagree: U1.79 (PD10); also elsewhere on the board
/mcu/BOT_ID_DISPLAY.TeamBlue: U1.22 (PF10); also elsewhere on the board
/mcu/BOT_ID_SWITCHES.IDX0: U1.126 (PG11); also elsewhere on the board
/mcu/BOT_ID_SWITCHES.IDX1: U1.125 (PG10); also elsewhere on the board
/mcu/BOT_ID_SWITCHES.IDX2: U1.115 (PD1); also elsewhere on the board
/mcu/BOT_ID_SWITCHES.IDX3: U1.114 (PD0); also elsewhere on the board
/mcu/BOT_ID_SWITCHES.SRC_PRIO_USER_~AUTO: U1.70 (PB11); also elsewhere on the board
/mcu/BOT_ID_SWITCHES.TEAM_BLUE_~YELLOW: U1.69 (PB10); also elsewhere on the board
/mcu/BTNS.BACK: U1.63 (PE10); also elsewhere on the board
/mcu/BTNS.DOWN: U1.68 (PE15); also elsewhere on the board
/mcu/BTNS.ENTER: U1.64 (PE11); also elsewhere on the board
/mcu/BTNS.LEFT: U1.65 (PE12); also elsewhere on the board
/mcu/BTNS.RIGHT: U1.66 (PE13); also elsewhere on the board
/mcu/BTNS.UP: U1.67 (PE14); also elsewhere on the board
/mcu/BUZZER: U1.5 (PE6); also elsewhere on the board
/mcu/DEBUG_MODE: R1.2, U1.7 (PC13)
/mcu/DIP.0: U1.49 (PF11); also elsewhere on the board
/mcu/DIP.1: U1.50 (PF12); also elsewhere on the board
/mcu/DIP.2: U1.53 (PF13); also elsewhere on the board
/mcu/DIP.3: U1.54 (PF14); also elsewhere on the board
/mcu/DIP.4: U1.55 (PF15); also elsewhere on the board
/mcu/DIP.5: U1.58 (PE7); also elsewhere on the board
/mcu/DIP.6: U1.59 (PE8); also elsewhere on the board
/mcu/DIP.7: U1.60 (PE9); also elsewhere on the board
/mcu/DOTSTARS.MOSI: U1.135 (PB5); also elsewhere on the board
/mcu/DOTSTARS.SCK: U1.133 (PB3(JTDO); also elsewhere on the board
/mcu/LEDS.1: U1.91 (PG6); also elsewhere on the board
/mcu/LEDS.2: U1.90 (PG5); also elsewhere on the board
/mcu/LEDS.3: U1.89 (PG4); also elsewhere on the board
/mcu/LEDS.4: U1.82 (PD13); also elsewhere on the board
/mcu/NRST: C13.1, J2.10 (~RESET), R2.2, SW2.2, U1.25 (NRST)
/mcu/ODIN.BOOT0: U1.124 (PG9); also elsewhere on the board
/mcu/ODIN.CTS: U1.117 (PD3); also elsewhere on the board
/mcu/ODIN.RTS: U1.118 (PD4); also elsewhere on the board
/mcu/ODIN.RX: U1.122 (PD6); also elsewhere on the board
/mcu/ODIN.TX: U1.119 (PD5); also elsewhere on the board
/mcu/ODIN.~DET: U1.110 (PA15(JTDI)); also elsewhere on the board
/mcu/ODIN.~RST: U1.123 (PD7); also elsewhere on the board
/mcu/OPTICAL_FLOW.BOOT0: U1.137 (PB7); also elsewhere on the board
/mcu/OPTICAL_FLOW.CTS: U1.76 (PB15); also elsewhere on the board
/mcu/OPTICAL_FLOW.RST: U1.136 (PB6); also elsewhere on the board
/mcu/OPTICAL_FLOW.RTS: U1.75 (PB14); also elsewhere on the board
/mcu/OPTICAL_FLOW.RX: U1.139 (PB8); also elsewhere on the board
/mcu/OPTICAL_FLOW.TX: U1.140 (PB9); also elsewhere on the board
/mcu/POWER.RX: U1.56 (PG0); also elsewhere on the board
/mcu/POWER.TX: U1.57 (PG1); also elsewhere on the board
/mcu/RCC_OSC32_N: C3.1, U1.9 (PC15), Y1.1
/mcu/RCC_OSC32_P: C4.1, U1.8 (PC14), Y1.2
/mcu/RCC_OSC_N: C11.1, U1.24 (PH1), Y2.1
/mcu/RCC_OSC_P: C12.1, U1.23 (PH0), Y2.3
/mcu/SDMMC1_CK: J1.5 (CLK), U1.113 (PC12)
/mcu/SDMMC1_CMD: J1.3 (CMD), U1.116 (PD2)
/mcu/SDMMC1_D0: J1.7 (DAT0), U1.98 (PC8)
/mcu/SDMMC1_D1: J1.8 (DAT1), U1.99 (PC9)
/mcu/SDMMC1_D2: J1.1 (DAT2), U1.111 (PC10)
/mcu/SDMMC1_D3: J1.2 (CD/DAT3), U1.112 (PC11)
/mcu/SHELL_DETECT.LIGHT: U1.13 (PF3); also elsewhere on the board
/mcu/SHELL_DETECT.RST: U1.12 (PF2); also elsewhere on the board
/mcu/SHELL_DETECT.SCL: U1.11 (PF1); also elsewhere on the board
/mcu/SHELL_DETECT.SDA: U1.10 (PF0); also elsewhere on the board
/mcu/SWCLK: J2.4 (SWCLK/TCK), U1.109 (PA14(JTCK)
/mcu/SWDIO: J2.2 (SWDIO/TMS), U1.105 (PA13(JTMS)
/mcu/USB_BOOT0_CONTROL: Q2.1 (G), R8.1, SW3.3
/mcu/USB_HS_D_N: P1.A7 (D-), P1.B7 (D-), U1.103 (PA11)
/mcu/USB_HS_D_P: P1.A6 (D+), P1.B6 (D+), U1.104 (PA12)
/mcu/USER_BOOT0_OVERRIDE: R6.1, SW3.4
/mcu/V_{sense}_3v3: R11.2, R14.1, U1.36 (PA2)
/mcu/V_{sense}_5V0: R10.2, R13.1, U1.35 (PA1)
/mcu/V_{sense}_V_{batt}: R9.2, R12.1, U1.34 (PA0)
GND: C1.2, C2.2, C3.2, C4.2, C5.2, C6.2, C7.2, C8.2, C9.2, C10.2, C11.2, C12.2, C13.2, C14.2, C15.2, C16.2, C17.2, C18.2, C19.2, C20.2, C21.2, C22.2, C23.2, C24.2, C25.2, C26.2, C27.2, J1.6 (VSS), J1.9 (Anchor), J2.3 (GND), J2.5 (GND), J2.9 (GNDDetect), P1.A1 (GND), P1.A12 (GND), P1.B1 (GND), P1.B12 (GND), P1.S1 (SHIELD), Q2.2 (S), R3.2, R7.2, R8.2, R12.2, R13.2, R14.2, R15.2, R126.2, SW2.1, U1.16 (VSS), U1.31 (VSSA), U1.38 (VSS), U1.51 (VSS), U1.61 (VSS), U1.83 (VSS), U1.94 (VSS), U1.107 (VSS), U1.120 (VSS), U1.130 (VSS), Y2.2, Y2.4; also elsewhere on the board
unnamed: C14.1, U1.71 (VCAP)
unnamed: C15.1, U1.106 (VCAP)
unnamed: P1.A5 (CC1), R15.1
unnamed: P1.B5 (CC2), R126.1
unnamed: Q1.1 (G), Q2.3 (D), R4.2
unnamed: Q1.2 (S), R5.2
unnamed: R1.1, R3.1, SW1.2
VBUS: P1.A4 (VBUS), P1.A9 (VBUS), P1.B4 (VBUS), P1.B9 (VBUS), SW3.2

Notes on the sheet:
DIP 2-3 closed: USB Plugged Enters Bootloader DIP 1-4 closed: Always Enter Bootloader All Open: Enter Program
USB Connection
MCU
Clocks
Debug Header
VDD Decoupling
Debug Mode Selector
Voltage Monitoring
Reset Logic
SD Card
MISO
Boot Mode Selection


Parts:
J9: Conn_01x10_MountingPin; JST_GH_SM10B-GHS-TB_1x10-1MP_P1.25mm_Horizontal
R44, R45, R48, R49: 100k; R_0402_1005Metric
R46, R47: 330; R_0402_1005Metric

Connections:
+3V3: J9.2, R44.1, R45.1; also elsewhere on the board
+5V: J9.1; also elsewhere on the board
/kicker/KICKER.BOOT0: J9.5, R49.1; also elsewhere on the board
/kicker/KICKER.CTS: J9.9, R44.2; also elsewhere on the board
/kicker/KICKER.RST: J9.6, R48.1; also elsewhere on the board
/kicker/KICKER.RTS: R47.1; also elsewhere on the board
/kicker/KICKER.RX: J9.8, R45.2; also elsewhere on the board
/kicker/KICKER.TX: R46.1; also elsewhere on the board
GND: J9.3, J9.4, J9.MP (MountPin), R48.2, R49.2; also elsewhere on the board
unnamed: J9.7, R46.2
unnamed: J9.10, R47.2

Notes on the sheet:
Kicker Connector

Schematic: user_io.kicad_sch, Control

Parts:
BZ1: MLT-5020
C32, C33, C34, C35, C36, C37: 0.1uF 63V; C_0402_1005Metric
C38: 4.7uF 25V; C_0805_2012Metric
D9: RBR5LAM60ATR; D_SOD-128
D10, D11, D12, D13: XL-1608UGC-04; LED0603
Q3: SI2310-TP; SOT-23
R84, R85, R86, R89, R90, R92, R93, R94, R95, R97, R107, R114, R115, R117: 330; R_0402_1005Metric
R87, R88, R96, R98, R99, R100, R101, R102, R103, R104, R105, R106, R108, R109, R110, R111, R112, R113, R116, R118: 10k; R_0402_1005Metric
R91: 10; R_0402_1005Metric
SW6: 219-8MST
SW7, SW8, SW9, SW10, SW11, SW12: B3F-1000
U4, U5, U6, U7, U8, U9, U10, U11, U12, U13, U14: SK9822

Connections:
+3V3: BZ1.1 (+), D9.1 (K), R87.2, R88.2, R106.2, R112.2, R113.2, R116.2, SW6.1, SW6.2, SW6.3, SW6.4, SW6.5, SW6.6, SW6.7, SW6.8; also elsewhere on the board
+5V: C38.2, U4.4 (VCC), U5.4 (VCC), U6.4 (VCC), U7.4 (VCC), U8.4 (VCC), U9.4 (VCC), U10.4 (VCC), U11.4 (VCC), U12.4 (VCC), U13.4 (VCC), U14.4 (VCC); also elsewhere on the board
/mcu/BTNS.BACK: R93.2; also elsewhere on the board
/mcu/BTNS.DOWN: R117.2; also elsewhere on the board
/mcu/BTNS.ENTER: R94.2; also elsewhere on the board
/mcu/BTNS.LEFT: R114.2; also elsewhere on the board
/mcu/BTNS.RIGHT: R115.2; also elsewhere on the board
/mcu/BTNS.UP: R107.2; also elsewhere on the board
/mcu/BUZZER: R91.1, R96.1; also elsewhere on the board
/mcu/DIP.0: R84.2; also elsewhere on the board
/mcu/DIP.1: R85.2; also elsewhere on the board
/mcu/DIP.2: R86.2; also elsewhere on the board
/mcu/DIP.3: R89.2; also elsewhere on the board
/mcu/DIP.4: R90.2; also elsewhere on the board
/mcu/DIP.5: R92.2; also elsewhere on the board
/mcu/DIP.6: R95.2; also elsewhere on the board
/mcu/DIP.7: R97.2; also elsewhere on the board
/mcu/DOTSTARS.MOSI: U4.1 (SDI); also elsewhere on the board
/mcu/DOTSTARS.SCK: R118.1, U4.2 (CKI); also elsewhere on the board
/mcu/LEDS.1: R111.1; also elsewhere on the board
/mcu/LEDS.2: R110.1; also elsewhere on the board
/mcu/LEDS.3: R109.1; also elsewhere on the board
/mcu/LEDS.4: R108.1; also elsewhere on the board
GND: C32.2, C33.2, C34.2, C35.2, C36.2, C37.2, C38.1, D10.1 (K), D11.1 (K), D12.1 (K), D13.1 (K), Q3.2 (S), R96.2, R98.1, R99.1, R100.1, R101.1, R102.1, R103.1, R104.1, R105.1, R118.2, SW7.3, SW8.3, SW9.3, SW10.3, SW11.3, SW12.3, U4.3 (GND), U5.3 (GND), U6.3 (GND), U7.3 (GND), U8.3 (GND), U9.3 (GND), U10.3 (GND), U11.3 (GND), U12.3 (GND), U13.3 (GND), U14.3 (GND); also elsewhere on the board
unnamed: BZ1.2 (-), D9.2 (A), Q3.3 (D)
unnamed: C32.1, R87.1, SW7.1
unnamed: C33.1, R88.1, SW8.1
unnamed: C34.1, R106.1, SW9.1
unnamed: C35.1, R112.1, SW10.1
unnamed: C36.1, R113.1, SW11.1
unnamed: C37.1, R116.1, SW12.1
unnamed: D10.2 (A), R108.2
unnamed: D11.2 (A), R109.2
unnamed: D12.2 (A), R110.2
unnamed: D13.2 (A), R111.2
unnamed: Q3.1 (G), R91.2
unnamed: R84.1, R98.2, SW6.16
unnamed: R85.1, R99.2, SW6.15
unnamed: R93.1, SW7.2
unnamed: R94.1, SW8.2
unnamed: R86.1, R100.2, SW6.14
unnamed: R89.1, R101.2, SW6.13
unnamed: R90.1, R102.2, SW6.12
unnamed: R92.1, R103.2, SW6.11
unnamed: R95.1, R104.2, SW6.10
unnamed: R97.1, R105.2, SW6.9
unnamed: R107.1, SW9.2
unnamed: R114.1, SW10.2
unnamed: R115.1, SW11.2
unnamed: R117.1, SW12.2
unnamed: U4.5 (CKO), U5.2 (CKI)
unnamed: U4.6 (SDO), U5.1 (SDI)
unnamed: U5.5 (CKO), U6.2 (CKI)
unnamed: U5.6 (SDO), U6.1 (SDI)
unnamed: U6.5 (CKO), U7.2 (CKI)
unnamed: U6.6 (SDO), U7.1 (SDI)
unnamed: U8.5 (CKO), U9.2 (CKI)
unnamed: U8.6 (SDO), U9.1 (SDI)
unnamed: U9.5 (CKO), U10.2 (CKI)
unnamed: U10.5 (CKO), U11.2 (CKI)
unnamed: U9.6 (SDO), U10.1 (SDI)
unnamed: U10.6 (SDO), U11.1 (SDI)
unnamed: U11.5 (CKO), U12.2 (CKI)
unnamed: U11.6 (SDO), U12.1 (SDI)
unnamed: U13.2 (CKI), U14.5 (CKO)
unnamed: U8.2 (CKI), U13.5 (CKO)
unnamed: U13.1 (SDI), U14.6 (SDO)
unnamed: U8.1 (SDI), U13.6 (SDO)
unnamed: U7.5 (CKO), U14.2 (CKI)
unnamed: U7.6 (SDO), U14.1 (SDI)

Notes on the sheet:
4x Motor 1x Radio 1x IMU 1x Kicker 1x Optical 1x Power 2x General Purpose
Dotstars
Robot Config
Debug Leds
Audio Indicators
User Buttons

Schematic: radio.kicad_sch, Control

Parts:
J5: BM10B-SRSS-TB; JST_SH_BM10B-SRSS-TB_1x10-1MP_P1.00mm_Vertical
R120, R121, R124, R125: 100k; R_0402_1005Metric
R122, R123: 330; R_0402_1005Metric

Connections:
+3V3: J5.9, R120.1, R121.1; also elsewhere on the board
+5V: J5.10; also elsewhere on the board
/mcu/ODIN.BOOT0: J5.7, R124.1; also elsewhere on the board
/mcu/ODIN.CTS: J5.4, R120.2; also elsewhere on the board
/mcu/ODIN.RTS: R123.1; also elsewhere on the board
/mcu/ODIN.RX: J5.5, R121.2; also elsewhere on the board
/mcu/ODIN.TX: R122.1; also elsewhere on the board
/mcu/ODIN.~DET: J5.2; also elsewhere on the board
/mcu/ODIN.~RST: J5.8, R125.1; also elsewhere on the board
GND: J5.1, J5.MP (MountPin), R124.2, R125.2; also elsewhere on the board
unnamed: J5.3, R123.2
unnamed: J5.6, R122.2

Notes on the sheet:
Radio Module Communication

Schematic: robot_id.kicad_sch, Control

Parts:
D3, D4, D6, D7: LTST-C195KGJRKT; LED0606_S_1324
D5: MHT194YBCT; LED0606_Z_1324
D8: XL-1608UOC-06; LED0603
J14: Conn_01x06; JST_GH_BM06B-GHS-TBT_1x06-1MP_P1.25mm_Vertical
R59, R60, R63, R64, R74, R75: 330; R_0402_1005Metric
R61, R62: 2.7k; R_0402_1005Metric
R65, R66, R67, R68, R69, R70, R71, R72, R73, R76, R77, R78, R79, R80, R81, R82, R83: 10k; R_0402_1005Metric
SW4: 221ADC16
SW5: SW_DIP_x02; 219-2MST

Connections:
+3V3: J14.1, R61.2, R62.2, R65.2, R66.2, R73.2, R79.2, R80.2, SW4.C, SW5.1, SW5.2; also elsewhere on the board
/mcu/BOT_ID_DISPLAY.BL: D6.2 (A2), D6.3 (K1); also elsewhere on the board
/mcu/BOT_ID_DISPLAY.BR: D7.2 (A2), D7.3 (K1); also elsewhere on the board
/mcu/BOT_ID_DISPLAY.FL: D3.2 (A2), D3.3 (K1); also elsewhere on the board
/mcu/BOT_ID_DISPLAY.FR: D4.2 (A2), D4.3 (K1); also elsewhere on the board
/mcu/BOT_ID_DISPLAY.SrcDisagree: R83.1; also elsewhere on the board
/mcu/BOT_ID_DISPLAY.TeamBlue: D5.2 (A2), D5.3 (K1); also elsewhere on the board
/mcu/BOT_ID_SWITCHES.IDX0: R64.2; also elsewhere on the board
/mcu/BOT_ID_SWITCHES.IDX1: R63.2; also elsewhere on the board
/mcu/BOT_ID_SWITCHES.IDX2: R60.2; also elsewhere on the board
/mcu/BOT_ID_SWITCHES.IDX3: R59.2; also elsewhere on the board
/mcu/BOT_ID_SWITCHES.SRC_PRIO_USER_~AUTO: R75.2; also elsewhere on the board
/mcu/BOT_ID_SWITCHES.TEAM_BLUE_~YELLOW: R74.2; also elsewhere on the board
/mcu/SHELL_DETECT.LIGHT: J14.5; also elsewhere on the board
/mcu/SHELL_DETECT.RST: J14.4; also elsewhere on the board
/mcu/SHELL_DETECT.SCL: J14.3, R62.1; also elsewhere on the board
/mcu/SHELL_DETECT.SDA: J14.2, R61.1; also elsewhere on the board
GND: D8.1 (K), J14.6, R67.1, R68.1, R69.1, R70.1, R71.1, R72.1, R76.1, R77.1, R78.1, R81.1, R82.1; also elsewhere on the board
unnamed: D3.1 (A1), R65.1
unnamed: D3.4 (K2), R71.2
unnamed: D4.1 (A1), R66.1
unnamed: D4.4 (K2), R72.2
unnamed: D5.1 (A1), R73.1
unnamed: D5.4 (K2), R76.2
unnamed: D6.1 (A1), R79.1
unnamed: D6.4 (K2), R81.2
unnamed: D7.1 (A1), R80.1
unnamed: D7.4 (K2), R82.2
unnamed: D8.2 (A), R83.2
unnamed: R64.1, R70.2, SW4.1
unnamed: R74.1, R77.2, SW5.4
unnamed: R75.1, R78.2, SW5.3
unnamed: R63.1, R69.2, SW4.4 (2)
unnamed: R60.1, R68.2, SW4.3 (4)
unnamed: R59.1, R67.2, SW4.6 (8)

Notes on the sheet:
Disagreement Warning
Dot Pattern Preview
Robot ID Selection
Shell ID Board Connector
Team Selection



Board: 6 copper layers, 148.0 x 86.0 mm, 243 parts (173 on the bottom side), 221 nets.

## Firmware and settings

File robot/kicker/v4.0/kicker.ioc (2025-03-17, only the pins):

Mcu.UserName=STM32G474VETx
PA0.GPIO_Label=SENSE_VBATT
PA0.Signal=ADC1_IN1
PA1.GPIO_Label=SENSE_VSW
PA1.Signal=ADC1_IN2
PA10.GPIO_Label=BOOT_USART1_RX
PA10.Signal=USART1_RX
PA11.GPIO_Label=BOOT_USART1_CTS
PA11.Signal=USART1_CTS
PA12.GPIO_Label=BOOT_USART1_RTS
PA12.Signal=USART1_RTS
PA13.Signal=SYS_JTMS-SWDIO
PA14.Signal=SYS_JTCK-SWCLK
PA15.Signal=I2C1_SCL
PA2.GPIO_Label=SENSE_5V
PA2.Signal=ADC1_IN3
PA3.GPIO_Label=SENSE_3V3
PA3.Signal=ADC1_IN4
PA4.GPIO_Label=FLASH_SPI1_NSS
PA4.Signal=SPI1_NSS
PA5.GPIO_Label=FLASH_SPI1_SCK
PA5.Signal=SPI1_SCK
PA6.GPIO_Label=FLASH_SPI1_MISO
PA6.Signal=SPI1_MISO
PA7.GPIO_Label=FLASH_SPI1_MOSI
PA7.Signal=SPI1_MOSI
PA9.GPIO_Label=BOOT_USART1_TX
PA9.Signal=USART1_TX
PB0.Signal=OPAMP3_VINP
PB1.Signal=OPAMP3_VOUT
PB10.GPIO_Label=DRIBBLER_USART3_TX
PB10.Signal=USART3_TX
PB13.GPIO_Label=DRIBBLER_USART3_CTS
PB13.Signal=USART3_CTS
PB14.GPIO_Label=DRIBBLER_USART3_RTS
PB14.Signal=USART3_RTS
PB15.GPIO_Label=HV_CHARGE
PB15.Signal=GPIO_Output
PB2.Signal=OPAMP3_VINM
PB3.GPIO_Label=BALL_SENSE_RST
PB3.Signal=GPIO_Output
PB5.GPIO_Label=USR_BTN
PB5.Signal=GPIO_Input
PB6.GPIO_Label=LED_SHUTDOWN_INITIATED
PB6.Signal=GPIO_Output
PB7.Signal=I2C1_SDA
PB8-BOOT0.GPIO_Label=BOOT0
PB8-BOOT0.Signal=GPIO_Input
PB9.GPIO_Label=LED_GREEN
PB9.Signal=GPIO_Output
PC0.GPIO_Label=BBL_AGPIO
PC0.Signal=ADC1_IN6
PC1.GPIO_Label=BBC_AGPIO
PC1.Signal=ADC1_IN7
PC10.GPIO_Label=I2C1_RST
PC10.Signal=GPIO_Output
PC11.GPIO_Label=I2C1_nDET
PC11.Signal=GPIO_Input
PC12.GPIO_Label=I2C1_INT
PC12.Signal=GPIO_Input
PC14-OSC32_IN.Signal=RCC_OSC32_IN
PC15-OSC32_OUT.Signal=RCC_OSC32_OUT
PC2.GPIO_Label=BBR_AGPIO
PC2.Signal=ADC1_IN8
PC3.GPIO_Label=VHV_SENSE
PC3.Signal=ADC1_IN9
PC6.Signal=I2C4_SCL
PC7.Signal=I2C4_SDA
PC8.Signal=I2C3_SCL
PC9.Signal=I2C3_SDA
PD0.GPIO_Label=DIP0
PD0.Signal=GPIO_Input
PD1.GPIO_Label=DIP1
PD1.Signal=GPIO_Input
PD10.GPIO_Label=I2C4_INT
PD10.Signal=GPIO_Input
PD11.GPIO_Label=I2C4_nDET
PD11.Signal=GPIO_Input
PD12.GPIO_Label=I2C4_RST
PD12.Signal=GPIO_Output
PD13.GPIO_Label=I2C3_INT
PD13.Signal=GPIO_Input
PD14.GPIO_Label=I2C3_nDET
PD14.Signal=GPIO_Input
PD15.GPIO_Label=I2C3_RST
PD15.Signal=GPIO_Output
PD2.GPIO_Label=DIP2
PD2.Signal=GPIO_Input
PD3.GPIO_Label=BALL_SENSE_USART2_CTS
PD3.Signal=USART2_CTS
PD4.GPIO_Label=BALL_SENSE_USART2_RTS
PD4.Signal=USART2_RTS
PD5.GPIO_Label=BALL_SENSE_USART2_TX
PD5.Signal=USART2_TX
PD6.GPIO_Label=BALL_SENSE_USART2_RX
PD6.Signal=USART2_RX
PD7.GPIO_Label=BALL_SENSE_BOOT0
PD7.Signal=GPIO_Output
PD8.GPIO_Label=HV_CHIP
PD8.Signal=GPIO_Input
PD9.GPIO_Label=HV_KICK
PD9.Signal=GPIO_Output
PE0.GPIO_Label=LED_RED
PE0.Signal=GPIO_Output
PE1.GPIO_Label=LED_BLUE
PE1.Signal=GPIO_Output
PE10.GPIO_Label=VSW_EN
PE10.Signal=GPIO_Output
PE11.GPIO_Label=VSW_PGOOD
PE11.Signal=GPIO_Input
PE13.GPIO_Label=DRIBBLER_BOOT0
PE13.Signal=GPIO_Output
PE14.GPIO_Label=DRIBBLER_RST
PE14.Signal=GPIO_Output
PE15.GPIO_Label=DRIBBLER_USART3_RX
PE15.Signal=USART3_RX
PE2.GPIO_Label=DOTSTAR_SPI4_SCK
PE2.Signal=SPI4_SCK
PE3.GPIO_Label=DOTSTAR_SPI4_NSS
PE3.Signal=SPI4_NSS
PE4.GPIO_Label=DIP3
PE4.Signal=GPIO_Output
PE5.GPIO_Label=DOTSTAR_SPI4_MISO
PE5.Signal=SPI4_MISO
PE6.GPIO_Label=DOTSTAR_SPI4_MOSI
PE6.Signal=SPI4_MOSI
PE8.GPIO_Label=USR_ADJ1
PE8.Signal=ADC3_IN6
PE9.GPIO_Label=USR_ADJ2
PE9.Signal=ADC3_IN2
PF0-OSC_IN.Signal=RCC_OSC_IN
PF1-OSC_OUT.Signal=RCC_OSC_OUT
PG10-NRST.GPIO_Label=NRST
PG10-NRST.Signal=GPIO_Input

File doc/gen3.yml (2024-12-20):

connectors:
  POWER-J1:
    type: XT-60
    subtype: female
    pinlabels: [VBATT, GND]
  CTRL-J1:
    type: XT-30
    subtype: male
    pinlabels: [VBATT, GND]
  BALL-J1:
    type: XT-30
    subtype: male
    pinlabels: [VBATT, GND]


cables:
  W1:
    gauge: 16 AWG
    length: 50 mm
    color_code: DIN
    wirecount: 2
    shield: false
    colors: [RD, BK]
  W2:
    gauge: 16 AWG
    length: 150 mm
    color_code: DIN
    wirecount: 2
    shield: false
    colors: [RD, BK]

connections:
  -
    - POWER-J1: [1,2]
    - W1: [1,2]
    - CTRL-J1: [1,2]
  -
    - POWER-J1: [1,2]
    - W2: [1,2]
    - BALL-J1: [1,2]

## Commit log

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2021-10-03 added 5V and 3v3
    [motorboard.kicad_sch]
2021-10-03 fixed power good pullups
    [motorboard.kicad_sch]
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2021-10-23 iniital bridge driver design
    [drive_motor_bridge_driver.kicad_sch, drive_motor_digital.kicad_sch, motorboard.kicad_sch]
2021-10-24 Magnetic Encoder Board Initial Commit
    [encoderboard.kicad_pcb, encoderboard.kicad_sch]
2021-10-24 Added input pull-down resistors in case SPI is unused
    [encoderboard.kicad_sch]
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2021-10-26 Changed UVW connector to a 3 pin; assigned packages to the connectors and the main IC
    [encoderboard.kicad_sch]
2021-10-26 Initial routing attempt to gauge rough board size
    [encoderboard.kicad_pcb]
2021-10-26 Assigned footprints for passive components and re-routed
    [encoderboard.kicad_pcb, encoderboard.kicad_sch]
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2021-10-29 drive and dribbler modules prototype
    [12v_universal_reg.kicad_sch, 3v3_5v0_reg.kicad_sch, dribbler_motor.kicad_sch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]
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2021-10-29 fixed mcu busses (I think, probably not)
    [12v_universal_reg.kicad_sch, 3v3_5v0_reg.kicad_sch, dribbler_motor.kicad_sch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]
2021-10-29 finished MCU, SD, LED, DIP, and Vbatt mon. cube_hal updated
    [drive_motor.kicad_sch, mcu.kicad_sch, motorboard.kicad_sch]
2021-11-01 added top level bus aliases, other top level dev
    [dribbler_motor.kicad_sch, drive_motor.kicad_sch, drive_motor_bridge_driver.kicad_sch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]
2021-11-03 power protection and power tree done
    [12v_universal_reg.kicad_sch, 3v3_5v0_reg.kicad_sch, drive_motor_bridge_driver.kicad_sch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]
2021-11-03 fixed duplicate pullup resistor
    [motorboard.kicad_sch]
2021-11-03 fixed duplicate reset switch, I think I should go to bed
    [motorboard.kicad_sch]
2021-11-04 added power and temp monitoring
    [motorboard.kicad_sch, power_protection.kicad_sch]
2021-11-04 replace RN with discrete, RN parts are weird
    [motorboard.kicad_sch, power_protection.kicad_sch]
2021-11-05 bus fixes
    [mcu.kicad_sch, power_protection.kicad_sch]
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2021-11-11 Changed layout: two M4 (4.4mm D) mounting holes 54mm apart
    [encoderboard.kicad_pcb]
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2021-11-12 initial motor schematic done
    [drive_motor_bridge_driver.kicad_sch, imu.kicad_sch, mcu.kicad_sch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]
2021-11-12 added STSPIN debug ports
    [motorboard.kicad_sch]
2021-11-12 cleaned up root schematic
    [motorboard.kicad_sch]
2021-11-12 cleaned up power protection schematic
    [motorboard.kicad_sch, power_protection.kicad_sch]
2021-11-13 bus name ERC fixes
    [12v_universal_reg.kicad_sch, 3v3_5v0_reg.kicad_sch, dribbler_motor.kicad_sch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]
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2021-11-15 cleaned up remaining schematics
    [12v_universal_reg.kicad_sch, 3v3_5v0_reg.kicad_sch, dribbler_motor.kicad_sch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]
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2021-11-15 added PDF and BOM export
    [motorboard.csv, motorboard.xml]
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2021-12-06 Added current limiting resistor and pull-down resistor to primary switch
    [motorboard.kicad_sch]
2021-12-06 Added pull-down resistors to each of the power enable pins
    [motorboard.kicad_sch]
2021-12-06 Revert "Added pull-down resistors to each of the power enable pins"
    This reverts commit 29f8b62b14b2a18fb2f6f2866531274844498572.
    [motorboard.kicad_sch]
2021-12-06 Added OV & UV threshold notes
    [power_protection.kicad_sch]
2021-12-06 Add bypass capacitor to +2.5V Ref & change 1M pull-down from the non-inverting input to the inverting input
    [power_protection.kicad_sch]
2021-12-16 Move 1M pull-down before the input filter
    [power_protection.kicad_sch]
2021-12-16 Add buffer to 2.5V reference
    [power_protection.kicad_sch]
2021-12-22 updated file formates to v6.0.0-rc2
    [12v_universal_reg.kicad_sch, 3v3_5v0_reg.kicad_sch, dribbler_motor.kicad_sch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]
2021-12-29 updated USB OGT power and some footprints
    [12v_universal_reg.kicad_sch, 3v3_5v0_reg.kicad_sch, dribbler_motor.kicad_sch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]
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2022-01-04 minor updates addressing DR feedback
    [12v_universal_reg.kicad_sch, drive_motor_bridge_driver.kicad_sch, drive_motor_digital.kicad_sch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]
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2022-02-27 Incomplete bodge-power-distribution schematics
    [12v_universal_reg.kicad_sch, 3v3_5v0_reg.kicad_sch, dribbler_motor.kicad_sch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]
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2022-05-01 Added JLC Fab Tooling Holes
    [encoderboard.kicad_pcb]
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2022-05-06 Separated power monitor into its own sheet
    [12v_universal_reg.kicad_sch, 3v3_5v0_reg.kicad_sch, power-distribution.kicad_sch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]
2022-05-06 Rename transistors library to AT-Transistors
    [12v_universal_reg.kicad_sch, 3v3_5v0_reg.kicad_sch, power-distribution.kicad_sch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]
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2022-10-27 Start implementation for soft-turn off
    [power-distribution.kicad_sch, power_protection.kicad_sch]
2022-11-01 Implement the key parts of the soft-turn off
    [power-distribution.kicad_sch, power_protection.kicad_sch]
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2022-11-02 Fixed PFET polarity
    [power-distribution.kicad_sch, power_protection.kicad_sch]
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2022-12-09 Minor aesthetics update; added 4 Green/Red LEDs for the dot pattern preview
    [indicators.kicad_sch, mcu.kicad_sch, power-distribution.kicad_pcb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]
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2022-12-09 Hole size change for a looser tolerance fit
    [power-distribution.kicad_pcb, power-distribution.kicad_sch]
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2023-01-19 Bodge Bot Kicker
    [ac-dc-kicker.kicad_pcb, ac-dc-kicker.kicad_sch]
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2023-01-30 schematic rework, add ball sense and WSD
    [digital.kicad_sch, flyback_charger.kicad_sch, kicker.kicad_sch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]
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2023-02-09 Control schematic (sans crystal oscillators)
    [control.kicad_sch, indicators.kicad_sch, load_switch.kicad_sch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]
2023-02-09 Label correction
    [mcu_filter_capacitors.kicad_sch]
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2023-02-28 Swap IMU to new connector
    [imu-breakout.kicad_pcb, imu-breakout.kicad_sch]
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2023-03-29 address initial issues with v1.0.0
    [digital.kicad_sch, flyback_charger.kicad_sch, kicker.kicad_pcb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]
2023-03-29 fix silkscreen DRC warning on Kicker v1.1.0
    [kicker.kicad_pcb]
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2023-04-21 kicker fixes, 1.1.0 tssop variant
    [digital.kicad_sch, flyback_charger.kicad_sch, kicker.kicad_pcb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]
2023-04-24 NEED KCv7.1 DRC check - silk and redundant routing fixed, v7.0
    [kicker.kicad_pcb]
2023-04-24 NEED v7.1 DRC CHECK - change default charge mode
    [flyback_charger.kicad_sch]
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2023-04-24 minor fixes to clear DRC
    [kicker.kicad_pcb]
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2023-05-02 radio v1.0.1 - fix LED footprint, add CTS/RTS solder mux
    [radio.kicad_pcb, radio.kicad_sch]
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2023-05-28 Diode & Rsense update; minor ERC fixes
    [digital.kicad_sch, flyback_charger.kicad_sch, kicker.kicad_pcb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]
2023-05-29 Consolidate 4.7uF capacitor variants into one BoM item
    [digital.kicad_sch, flyback_charger.kicad_sch, kicker.kicad_pcb]
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2023-05-29 Fixed back resistor value
    [breakbeam-emitter.kicad_sch]
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2023-07-27 readme updates, soldering guide, and errata for comp 2023 release
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2023-11-17 component/footprint swaps, layout work
    [flyback_charger.kicad_sch, hv_kicker.kicad_sch, kicker.kicad_pcb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]
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2023-11-22 fix HV net class spacing rules
    [kicker.kicad_pcb]
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2023-12-06 finish schematic fixes from the design review, layout work
    [digital.kicad_sch, flyback_charger.kicad_sch, hv_kicker.kicad_sch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]
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2024-04-21 kicker fixes
    [breakbeam.kicad_sch, digital.kicad_sch, kicker.kicad_sch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]
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2024-04-25 Fix connector part number
    [air_dribbler.kicad_sch]
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2024-05-05 Centered grid origin, updated footprints, and exported CAD model
    [radio.kicad_pcb, radio.step]
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2024-05-24 Swap TX/RX through isolator
    [isol.kicad_sch]
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2024-05-24 Add power status LEDs and resolved ERC errors
    [digital.kicad_sch, flyback_charger.kicad_sch, isol.kicad_sch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]
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2024-08-02 initial commit of power pinout and power files
    [power.kicad_pcb, power.kicad_sch]
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2024-11-04 fix bus aliasing issues
    [input_connectors.kicad_sch, mcu.kicad_sch, power.kicad_sch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]
2024-11-04 swap power fets
    [LM5069_Design_Calculator_REV_C__BSC070N10NS5.xlsx, power_protection.kicad_sch, power_regulation.kicad_sch]
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2024-11-15 fix 5V local AGAIN
    [power_regulation.kicad_sch]
2024-11-15 fix power flag ERC conflict
    [power_regulation.kicad_sch]
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2024-11-15 Revert "Merge branch 'main' of github.com:SSL-A-Team/electrical"
    This reverts commit e3e905e086ad656dbe27eb1d7768ff8b77b20f23, reversing
    changes made to b918b4ecffb897a591c7a6949e309c7e6ea46d1e. Merge broke
    schematics.
    [power.kicad_pcb, power_regulation.kicad_sch]
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2024-11-26 kicker power rework
    [ball_sense.kicad_sch, breakbeam.kicad_sch, digital.kicad_sch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]
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2024-12-20 update values in current sense spice sim and reflect in schematic
    [motor_driver.kicad_sch]
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2024-12-28 add TVS, update fusing, remove LDO body diode
    [encoder.kicad_sch, motor-controller.kicad_pcb, motor-controller.kicad_sch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]
2024-12-28 remove TLV 3v0 body diode, update 3v0 fusing
    [kicker.kicad_sch, mcu.kicad_sch, optical_flow.kicad_sch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]
2024-12-28 update fusing and remove diode on 3v0 supply
    [ball_sense.kicad_sch, breakbeam.kicad_sch, digital.kicad_sch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]
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2024-12-30 update boot mode docs, schematic visual fixes, UART default state fixes
    [display.kicad_sch, drive_motor.kicad_sch, imu.kicad_sch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]
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2025-01-20 fix power output connector and 3v3 local en pullup
    [input_connectors.kicad_sch, mcu.kicad_sch, mechanical.kicad_sch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]
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2025-01-29 fix SD pinout, routing work
    [control.kicad_pcb, mcu.kicad_sch]
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2025-03-13 Update schematic with updated symbol to resolve ERC
    [digital.kicad_sch]
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2025-03-17 fixed old conenctors
    [ball_sense.kicad_sch, breakbeam.kicad_sch, digital.kicad_sch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]
2025-03-17 layout after connector fix done
    [kicker.kicad_pcb]
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2025-04-08 fix hall silk on motor controller
    [motor-controller.kicad_pcb]
2025-04-08 fix xt30 and vertical data connector on schemnatic
    [ball_sense.kicad_sch, digital.kicad_sch, dribbler.kicad_sch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]
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2025-04-18 fixed to kicker v4
    [BOM-kicker.csv, flyback_charger.kicad_sch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]
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2025-07-27 update motor controller current sense and Vmotor protections
    [TempMotorPCB - TempMotorPCB.dxf, encoder.kicad_sch, mechanical.kicad_sch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]
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2026-01-28 fixed amplifier schematic
    [motor_driver.kicad_sch]
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2026-04-04 Changed BoM to use thin film resistors instead of thick film ones on the current sense amplifier
    [motor-controller.kicad_pcb]
2026-04-05 minor tweaks to pass DRC with courtyard updates, fab products
    [BOM-motor-controller.csv, mechanical.kicad_sch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]
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
